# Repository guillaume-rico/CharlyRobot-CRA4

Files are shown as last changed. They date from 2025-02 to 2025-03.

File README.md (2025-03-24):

# CharlyRobot-CRA4

# Carte de puissance

Analyse de la carte de puissance :

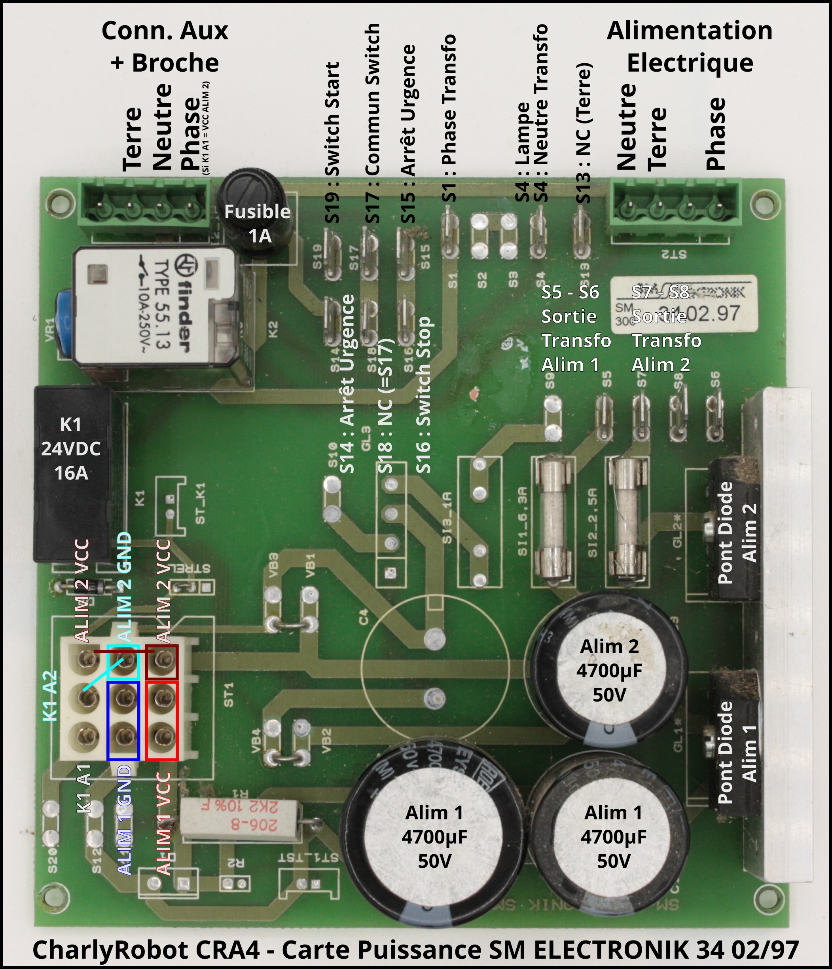
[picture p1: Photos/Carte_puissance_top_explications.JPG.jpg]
Description Carte de puissance


ALIM 1 :

 * Tension sortie transformateur : 23.6VAC
 * Tension sortie : 31VDC

ALIM 2 :

 * Tension sortie transformateur : 21VAC
 * Tension sortie : 28VDC

[Schématique](/carte_puissance/carte_puissance_schematique.pdf)

[PCB](/carte_puissance/carte_puissance_PCB.pdf)

# Indicateurs lumineux

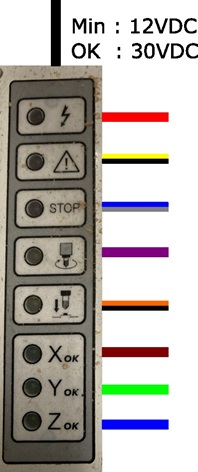
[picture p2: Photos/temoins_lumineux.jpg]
Témoins Lumineux


Tension d'alimentation : 12VDC -> 32VDC
Courant : 
 * 6mA pour 12VDC
 * 20mA pour 30VDC

| Témoin | Couleur fil |
| --- | --- |
| Masse commune | Noir |
| Alimentation électrique | Rouge |
| Alarme | Jaune / Noir |
| STOP | Bleu / Gris |
| Broche / Spindle | Violet |
| Capteur Outil | Orange / Noir |
| X Ok | Marron |
| Y Ok | Vert |
| Z Ok | Bleu |

# Carte de commande

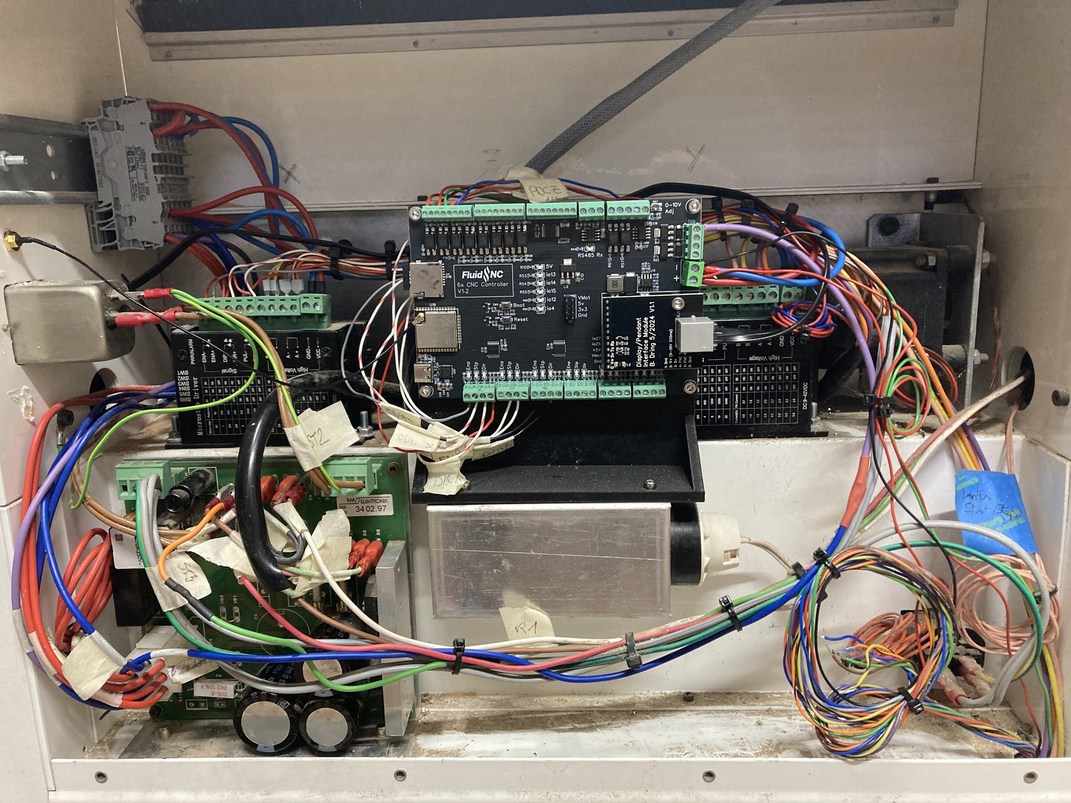
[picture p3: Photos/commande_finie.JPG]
commande_finie


La position des capteurs fin de course (1 seul par axe) :

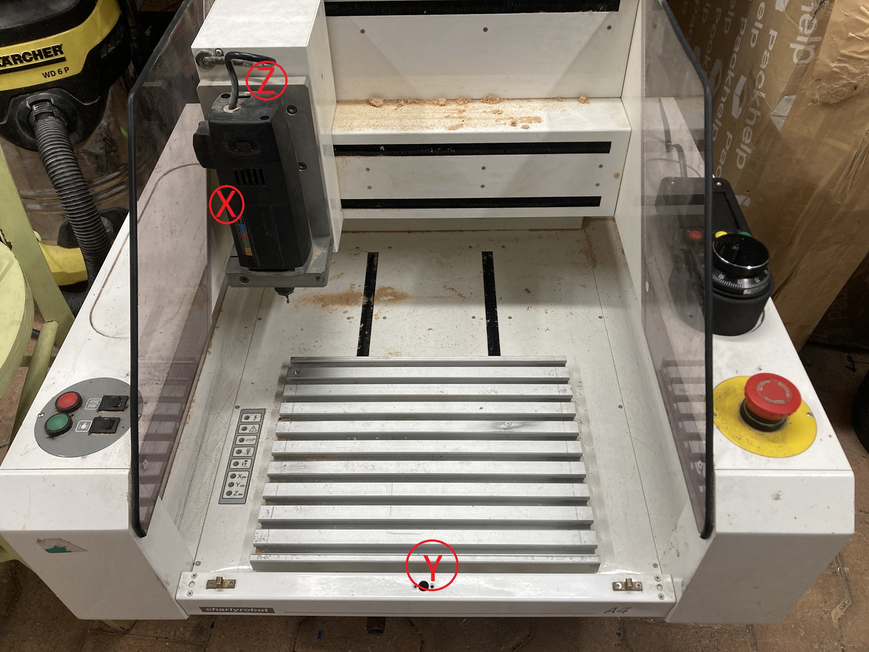
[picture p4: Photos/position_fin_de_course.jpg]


## Drivers commande moteur pas à pas 

C'est des drivers TB6600.
4 microstep (donc 800 steps par tour).
3A pour X et Y , 2A pour Z

Positionnement des switch :

| Switch | Valeur |
| --- | --- |
| S1 | ON |
| S2 | OFF |
| S3 | OFF |
| S4 | Z : ON |
| S5 | Y et Y : ON |
| S6 | OFF |

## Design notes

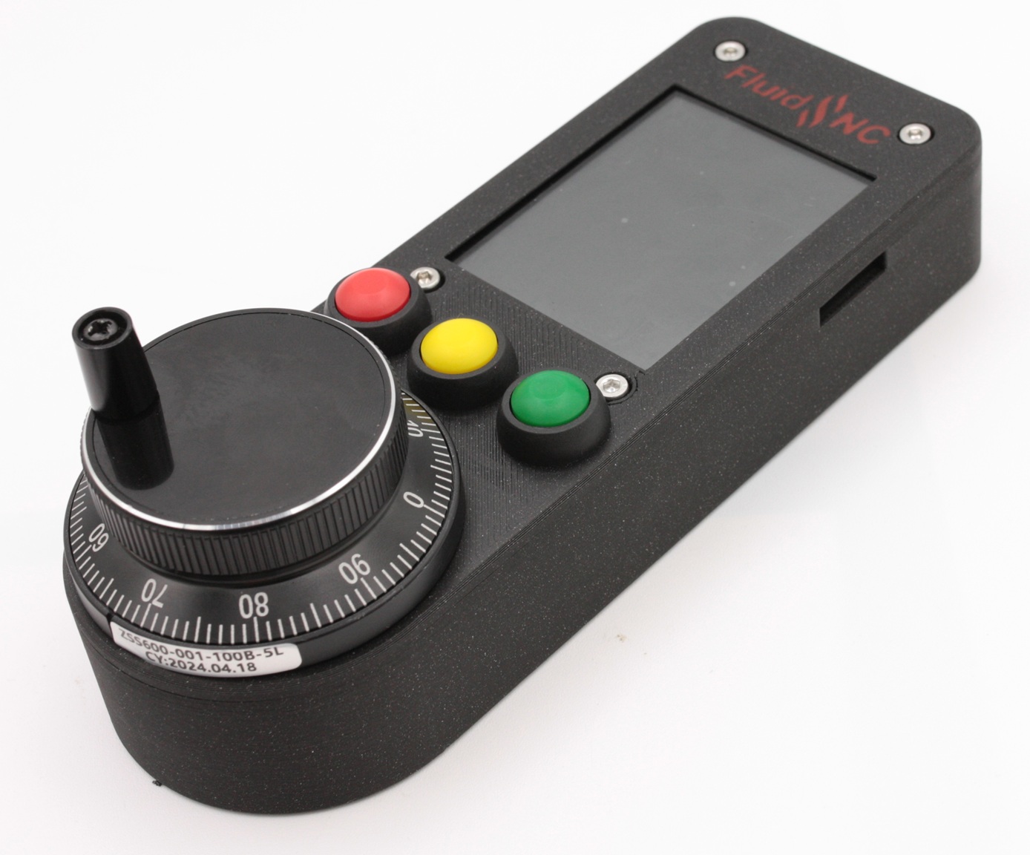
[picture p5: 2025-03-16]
Photos/CYD_CNC Handwheel Encoder_buttons.JPG

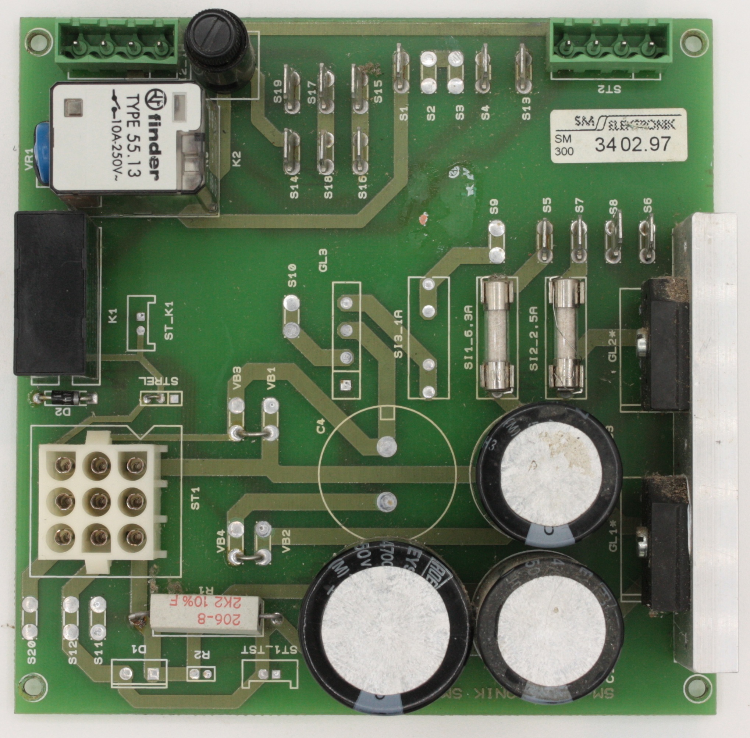
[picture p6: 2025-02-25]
Photos/Carte_puissance_top.JPG

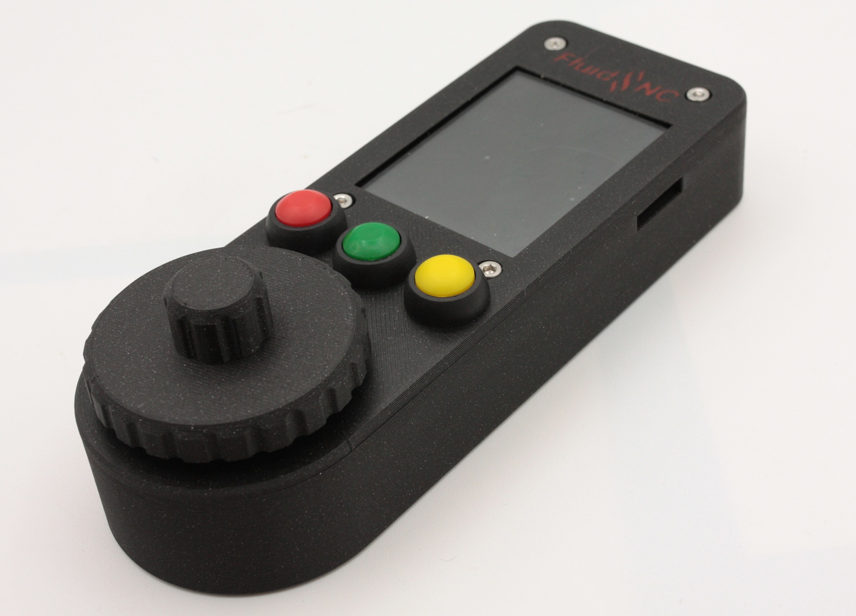
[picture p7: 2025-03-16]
Photos/CYD_small rotary encoder_buttons.JPG

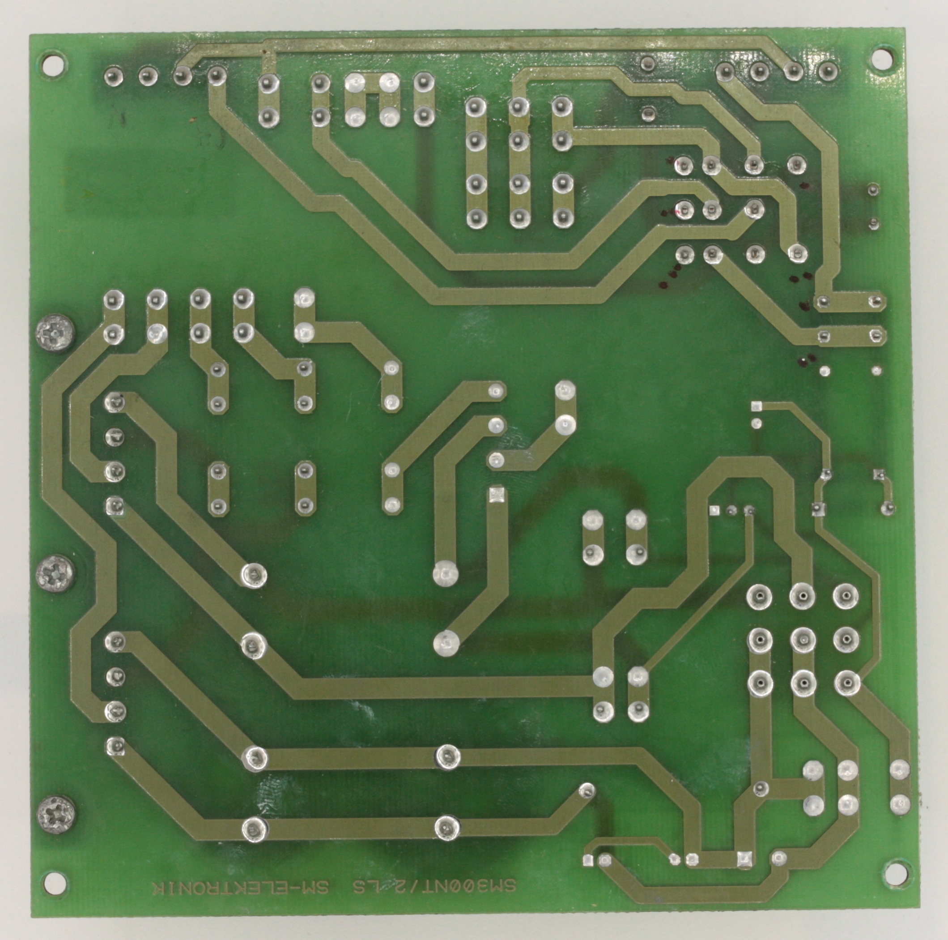
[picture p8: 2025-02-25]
Photos/Carte_puissance_bottom.JPG

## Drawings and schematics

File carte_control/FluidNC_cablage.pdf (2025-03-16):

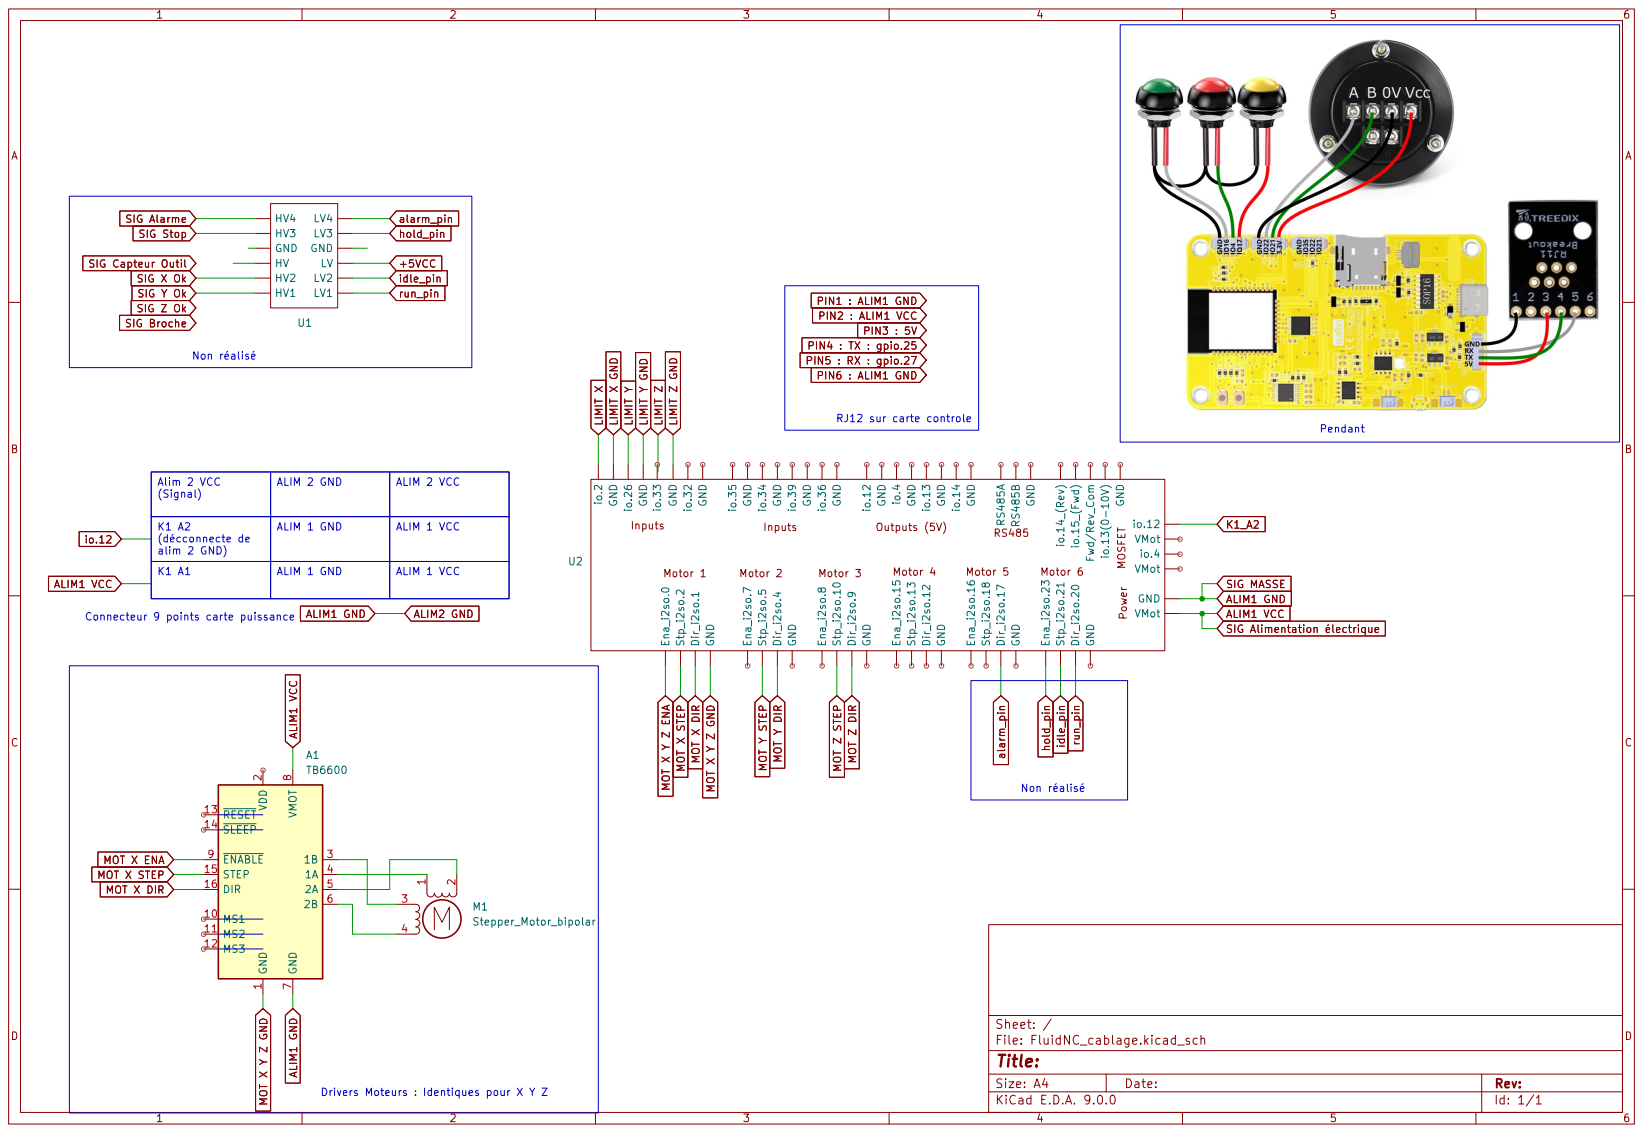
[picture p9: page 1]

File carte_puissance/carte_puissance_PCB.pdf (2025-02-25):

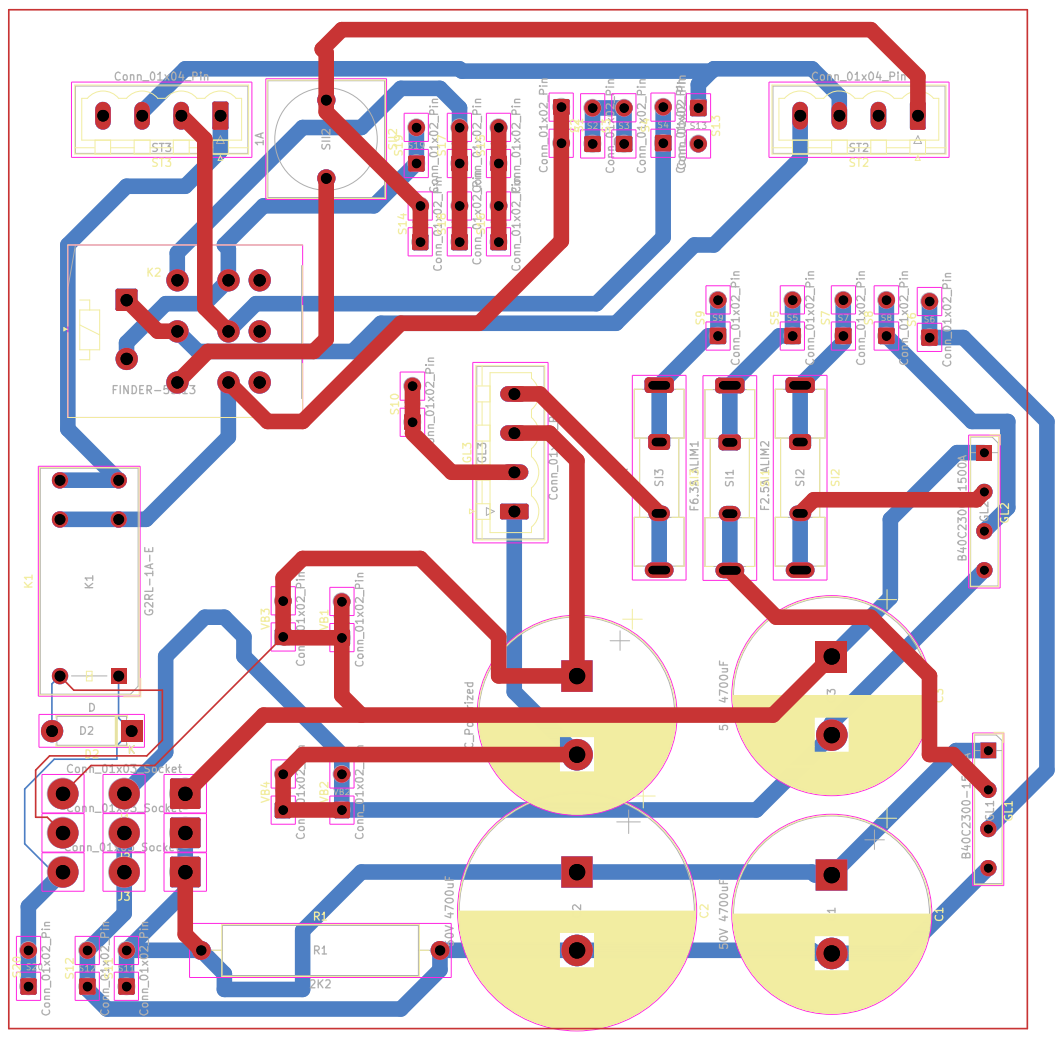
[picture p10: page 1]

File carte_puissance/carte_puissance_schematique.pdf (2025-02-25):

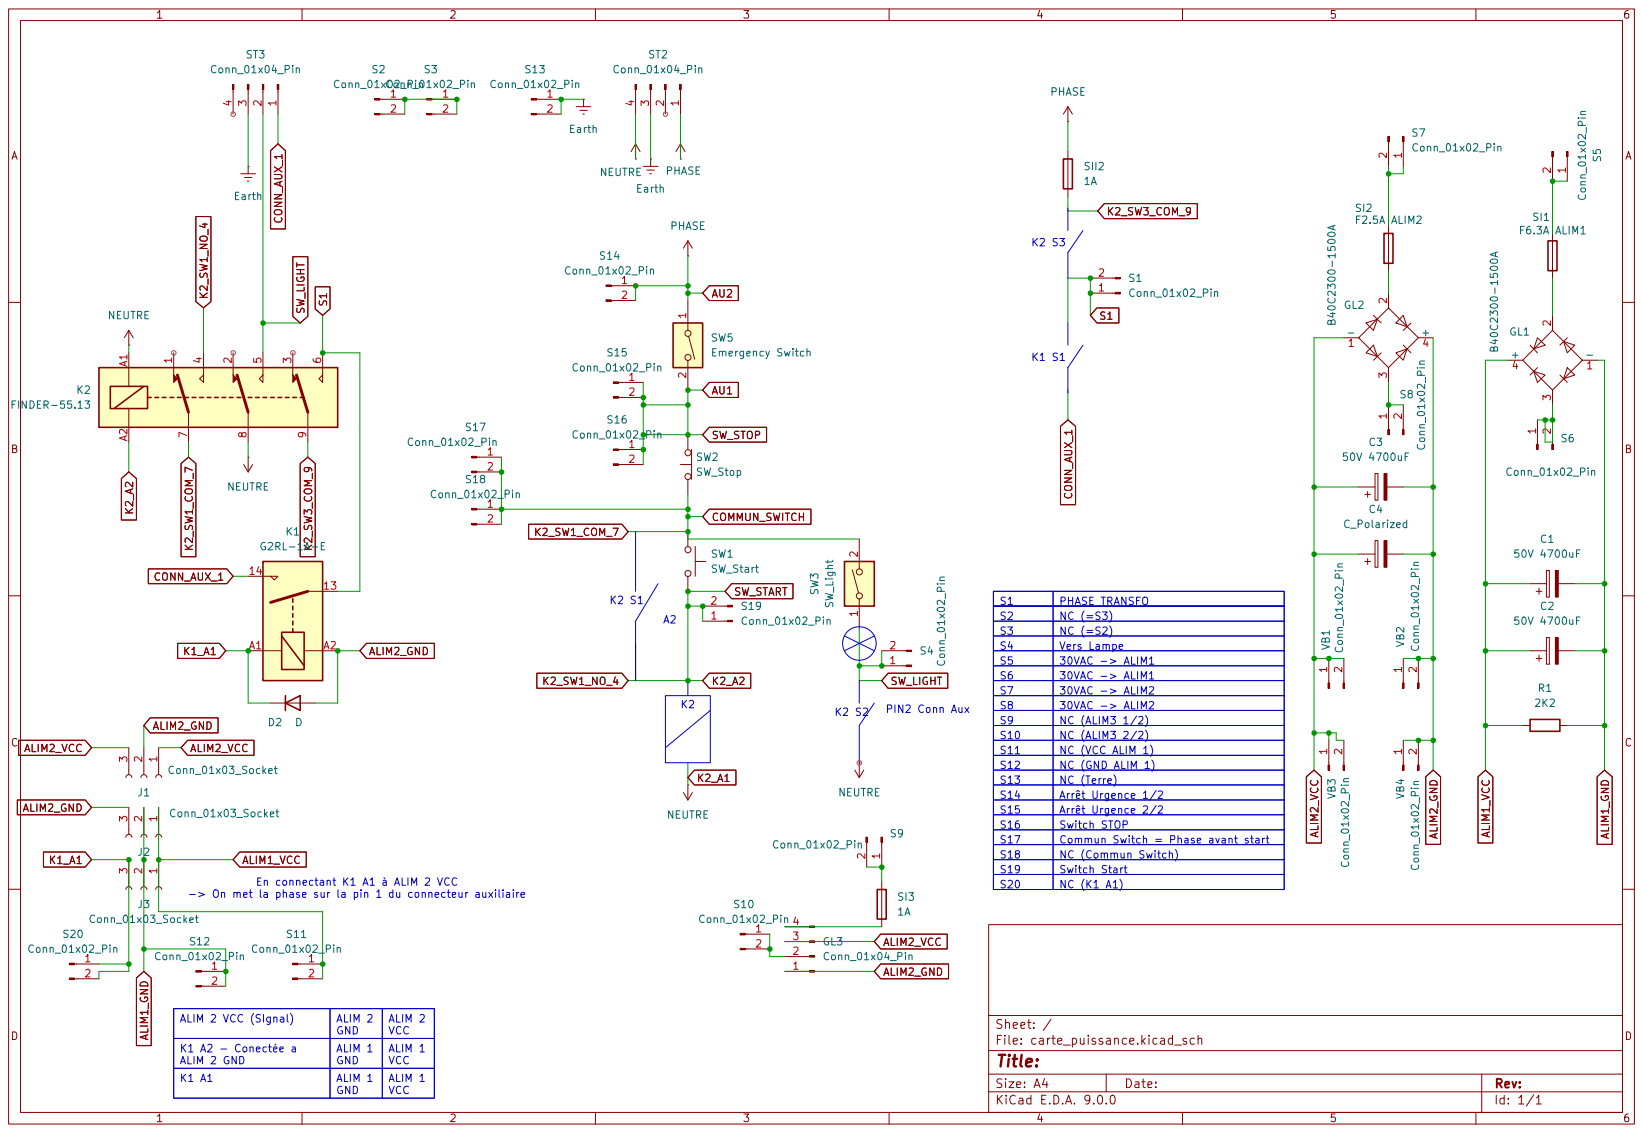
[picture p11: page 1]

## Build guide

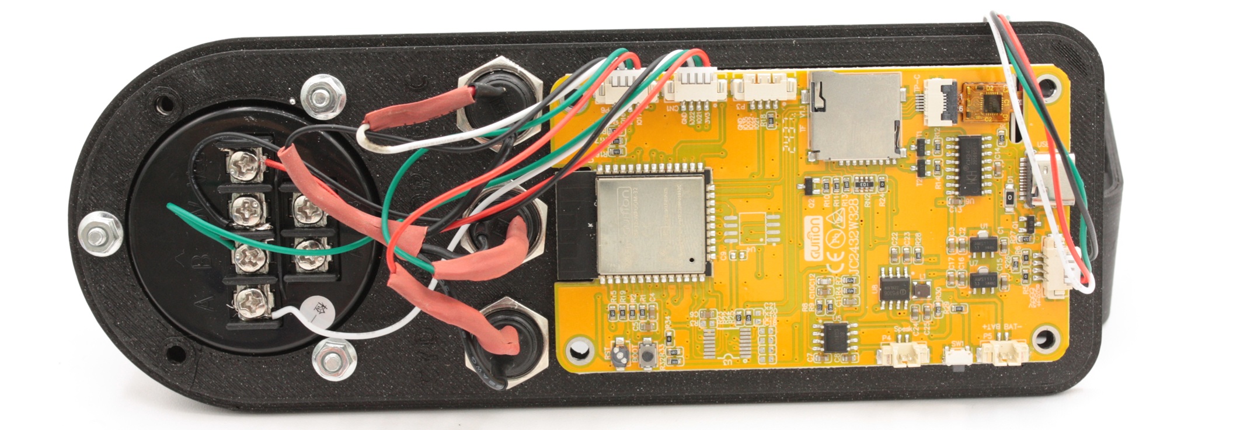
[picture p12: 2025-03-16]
Photos/pedndant_wiring_buttons.JPG

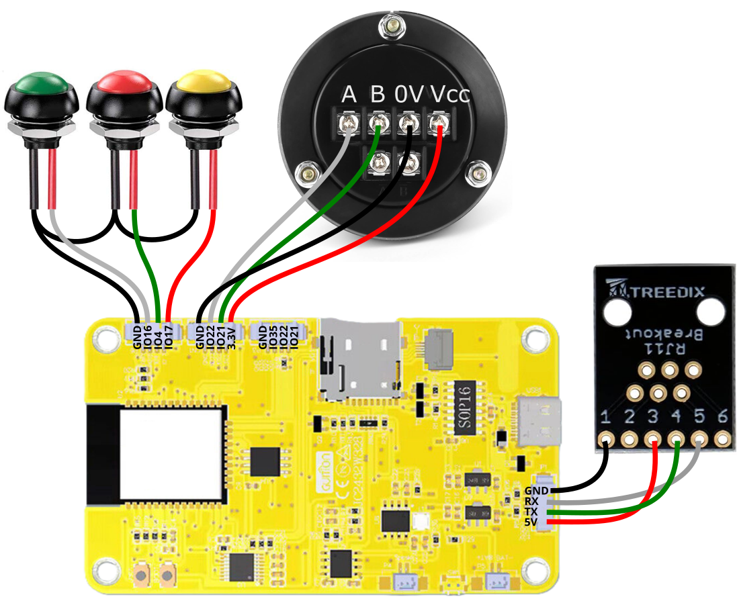
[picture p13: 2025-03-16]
carte_pendant/cyd_wiring_handwheel_button_v2.png

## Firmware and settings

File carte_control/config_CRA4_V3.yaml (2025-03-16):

board: 6x CNC Controller
name: CRA4
stepping:
  engine: I2S_STREAM
  idle_ms: 255
  pulse_us: 4
  dir_delay_us: 1
  disable_delay_us: 0
axes:
  shared_stepper_disable_pin: i2so.0
  x:
    steps_per_mm: 160
    max_rate_mm_per_min: 1000
    acceleration_mm_per_sec2: 100
    max_travel_mm: 310
    soft_limits: false
    homing:
      cycle: 2
      positive_direction: false
      mpos_mm: 0
      feed_mm_per_min: 100
      seek_mm_per_min: 1000
      settle_ms: 500
      seek_scaler: 1.1
      feed_scaler: 1.1
    motor0:
      limit_neg_pin: gpio.2:pu
      limit_pos_pin: NO_PIN
      limit_all_pin: NO_PIN
      hard_limits: true
      pulloff_mm: 2
      standard_stepper:
        step_pin: i2so.2
        direction_pin: i2so.1
        disable_pin: NO_PIN
  y:
    steps_per_mm: 160
    max_rate_mm_per_min: 1000
    acceleration_mm_per_sec2: 100
    max_travel_mm: 250
    soft_limits: false
    homing:
      cycle: 2
      positive_direction: true
      mpos_mm: 250
      feed_mm_per_min: 100
      seek_mm_per_min: 1000
      settle_ms: 500
      seek_scaler: 1.1
      feed_scaler: 1.1
    motor0:
      limit_neg_pin: NO_PIN
      limit_pos_pin: gpio.26:pu
      limit_all_pin: NO_PIN
      hard_limits: true
      pulloff_mm: 2
      standard_stepper:
        step_pin: i2so.5
        direction_pin: i2so.4:low
        disable_pin: NO_PIN
  z:
    steps_per_mm: 160
    max_rate_mm_per_min: 2000
    acceleration_mm_per_sec2: 100
    max_travel_mm: 300
    soft_limits: false
    homing:
      cycle: 1
      positive_direction: true
      mpos_mm: 150
      feed_mm_per_min: 100
      seek_mm_per_min: 1000
      settle_ms: 500
      seek_scaler: 1.1
      feed_scaler: 1.1
    motor0:
      limit_neg_pin: NO_PIN
      limit_pos_pin: gpio.33:pu
      limit_all_pin: NO_PIN
      hard_limits: true
      pulloff_mm: 1
      standard_stepper:
        step_pin: i2so.10
        direction_pin: i2so.9
        disable_pin: NO_PIN
i2so:
  bck_pin: gpio.22
  data_pin: gpio.21
  ws_pin: gpio.17
spi:
  miso_pin: gpio.19
  mosi_pin: gpio.23
  sck_pin: gpio.18
sdcard:
  card_detect_pin: NO_PIN
  cs_pin: gpio.5
probe:
  pin: gpio.39:low
  toolsetter_pin: gpio.36:low
coolant:
  mist_pin: gpio.4
  delay_ms: 0
start:
  must_home: false
relay:
  direction_pin: NO_PIN
  output_pin: gpio.12
  enable_pin: NO_PIN
  disable_with_s0: false
  s0_with_disable: true
  spinup_ms: 1000
  spindown_ms: 500
  tool_num: 0
  speed_map: 0=0.000% 0=100.000% 1=100.000%
  off_on_alarm: false
  
status_outputs:
  report_interval_ms: 500
  idle_pin: i2so.21
  run_pin: i2so.20
  hold_pin: i2so.23
  alarm_pin: i2so.17
  
uart1:
  txd_pin: gpio.25
  rxd_pin: gpio.27
  rts_pin: NO_PIN
  cts_pin: NO_PIN
  baud: 1000000
  mode: 8N1
uart_channel1:
  report_interval_ms: 75
  uart_num: 1
